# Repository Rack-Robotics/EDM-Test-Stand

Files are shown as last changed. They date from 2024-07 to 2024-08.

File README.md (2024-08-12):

# EDM Test Test

## Summary
This repository contains the documentation and resources for the EDM Test Rig, a test stand developed for advancing Electrical Discharge Machining (EDM) technology. The rig is designed to facilitate the development and testing of EDM components and systems. 

**Subassemblies of EDM Test Rig**
| Subassembly | Description | 
|---|---|
| Frame | Physical 4040 extrusion frame |
| DIN Rail Box | Mounts PSUs and control systems on DIN rails |
| Kinematics | Provides movement of EDM test items | 

## EDM Test Rig Specifications
Specifications of EDM Test rig.
| Specification | Description |
|---|---|
| Approximate Cost  | 2,000 USD |
| Size | 1.4 m x 0.58 m x 1.4 m | 
| Construction | 40x40, 20x20 Extruded Aluminum | 
| Kinematics | C7-Class Ballscrews + NEMA23 Stepper Motors |
| Linear Resolution | +- 30 Microns Maximum | 
| 3D Printer | FDM, Bambu Labs X1C | 
| Power | 120 VAC, 60 Hz |
| Firmware | DangerKlipper | 
| Operating System  | Linux | 
| DIN Rail Space | 40", 35 mm wide, 7.5 mm tall | 
| On-Board Power | 48 VDC, 24 VDC, 12 VDC, 5 VDC |

## Frame 
The frame provides a rigid, industrial grade, structure for conducting testing. 

### Frame Bill of Materials 

Hardware for frame. 
NOTE: 4040 Extrusions must be cut to length
| Item | Description | Quantity | Link | 
|---|---|---|---|
| 4040 Extrusions, Length  500 mm | 4040 Aluminum T-Slot Extrusion | 4 | [Amazon](https://a.co/d/1AEJy0P) |
| 4040 Extrusions, Length  500 mm, Countersunks | Extrusion w/ M5 Countersinks | 2 | [Amazon](https://a.co/d/1AEJy0P) |
| 4040 Extrusions, Length  1000 mm | 4040 Aluminum T-Slot Extrusion | 6 | [Amazon](https://a.co/d/1AEJy0P) |
| 4040 Extrusions, Length  1220 mm | 4040 Aluminum T-Slot Extrusion | 4 | [Amazon](https://a.co/d/1AEJy0P) |
| 4040 L Plate Bracket | M8x16 Brackets for 4040 Exturions | 1 Pack of 8 | [Amazon](https://a.co/d/fb5n5l8) | 
| 4040 L Bracket | Corner Bracket for 4040 Extruions | 1 Pack of 12  | [Amazon](https://a.co/d/0dLhwZp) | 
| 4040 Adjustable Feet | Adjustable feed for 4040 Extruions | 1 Pack of 4 | [Amazon](https://a.co/d/1duonmF) |

## DIN Rail Box
The DIN rail box provides 40 inches of 35 mm x 7.5 mm DIN rail space for mounting power supply units (PSUs), control systems, and other equipment. This setup ensures organized and efficient management of components within the EDM Test Rig.

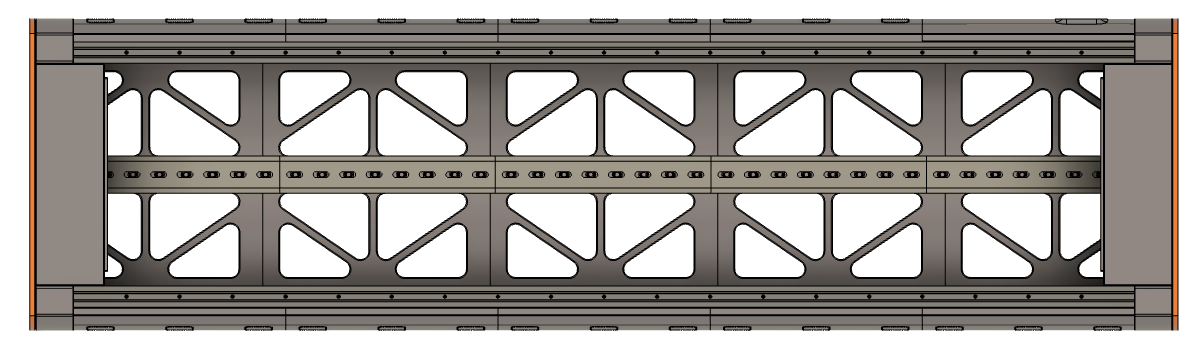
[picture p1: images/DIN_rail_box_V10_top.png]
DIN Rail Box

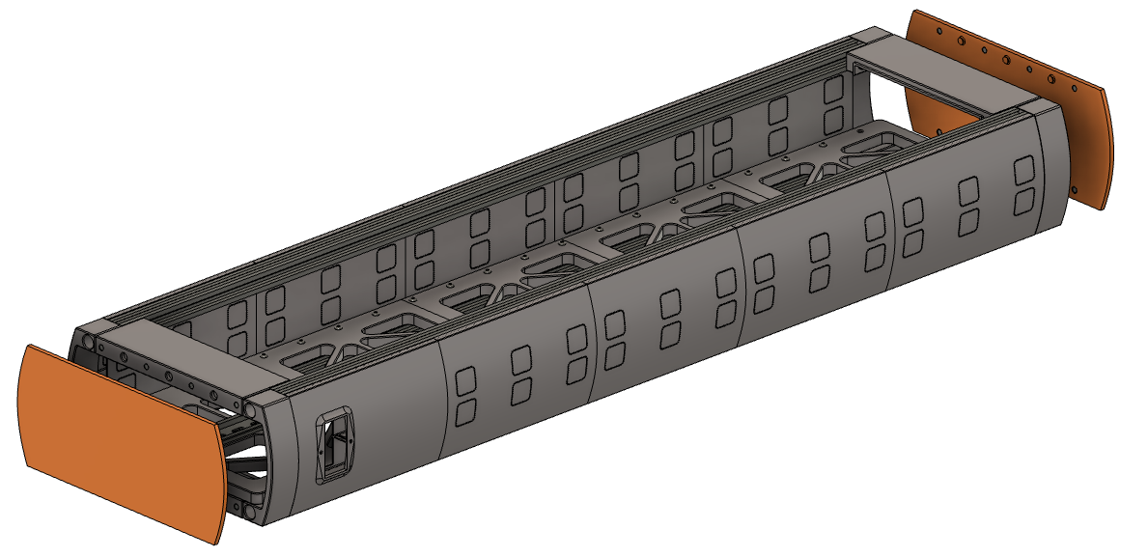
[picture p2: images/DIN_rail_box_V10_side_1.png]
DIN Rail Box


Note: The CAD models for the 2020 aluminum extrusions do not use T-slot nuts, but M4 taps. However, T-slot nuts are recommended.  

### DIN Rail Box Bill of Materials
Required FDM 3D prints for DIN rail box. This project requires several kilograms of filament. Print components with a brim to prevent warping. Enable ironing of top surfaces for base plates for a better surface quality. 
| 3D Prints | Description | Quantity | Material |
|---|---|---|---|
| Base Plate | Connects DIN rails to extrusions | 5 | PLA or ASA |
| Top Spacer | Connects adjacent extrusions | 2 | PLA or ASA |
| End Brace | Braces adjacent extrusions | 4 | PLA or ASA |
| PEM Cover | Mounts PEM module to side | 1 | PLA or ASA |
| Side Cover | Enclosure, with knockouts for wiring | 9 | PLA or ASA |
| End Cover | Enclosure, magnetically retained | 2 | PLA or ASA |

Hardware for DIN rail box: DIN rails, 2020 Aluminum extrusions, & Fasteners. 
| Item | Description | Quantity | Link | 
|---|---|---|---|
| DIN Rails | 35 mm x 7.5 mm, 8" long | 5 | [Amazon](https://a.co/d/1iSyUIB) |
| 2020 Aluminum Extrusion | 1 Meter Length, M6 end taps | 4 | [Amazon](https://a.co/d/0wJvInG) |
| Ruthex M5x9.5 mm Heat Set Insert | Heat set insert for DIN Rails | 15 | [Amazon](https://a.co/d/3ARX3Ab) |
| T-Nuts for 2020 Extrusions | For mounting to 2020 extrusions | 46 | [Amazon](https://a.co/d/hXSw9K0) |
| Neodymium Magnets, 6 mm OD x 2 mm | For magnetic end covers, super glued | 32 | [Amazon](https://a.co/d/eC7ES1e) |
| M6x1 mm, 16 mm Long, DIN 7991 | For 2020 Extrusions & End Spacers | 4 | [McMaster-Carr](https://www.mcmaster.com/91263A838/)  |
| M5x0.5 mm, 10 mm Long, ISO 7380-1 | For DIN rails and Base Plates | 15 | [McMaster-Carr](https://www.mcmaster.com/90943A117/)  | 
| M4x0.7 mm, 12 mm Long, DIN 7991 | For End Braces | 16 | [McMaster-Carr](https://www.mcmaster.com/91263A829/)  |
| M4x0.7 mm, 16 mm Long, ISO 7380 | For mounting base plates to extrusions | 30 | [McMaster-Carr](https://www.mcmaster.com/92095A194/)  |
| M3x0.5 mm. 30 mm Long, DIN 7991 | For PEM module | 2 | [McMaster-Carr](https://www.mcmaster.com/91294A141) |
| M3x0.5 mm Nut, DIN 934 | For PEM module | 2 | [McMaster-Carr](https://www.mcmaster.com/90591A250/)  |

Electronics components for DIN rail box. Includes the control board and computer for running Klipper/DangerKlipper + Linux. 
| Electronics Components | Description | Quantity | Link | 
|---|---|---|---|
| PEM Module | 15A 250V, with Rocker Switch | 1 | [Amazon](https://a.co/d/7NT5VqQ) |
| Meanwell LRS-350-48 | SMPS, 48 VDC | 1 | [Amazon](https://a.co/d/htJ3c0g) |
| Meanwell LRS-350-24 | SMPS, 24 VDC | 1 | [Amazon](https://a.co/d/2wwYgQc) |
| Meanwell LRS-350-12 | SMPS, 12 VDC | 1 | [Amazon](https://a.co/d/iZRj0RO) | 
| Meanwell LRS-100-5 | SMPS. 5 VDC | 1 | [Amazon](https://a.co/d/5YXJFhb) |
| SSR (optional) | 3-32 VDC, 24-480 VAC SSR | 1 | [Amazon](https://a.co/d/i7fY0Kh) |
| NEMA 5-15R Module (optional) | Breakout module for AC interconnects | 1 | [Amazon](https://a.co/d/cqJR1Gi) |
| M4 Ring terminal | 16-22 AWG Crimp, M4 (LRS PSU Terminal) | 100 | [Digikey](https://www.digikey.com/short/3vvnmc7q) |
| 16 AWG Wire, Stranded, Black | For AC & DC interconnects | 25' | [Digikey](https://www.digikey.com/en/products/detail/cnc-tech/1569-16-1-0500-001-1-TS/9450423) |
| 16 AWG Wire, Stranded, White | For AC interconnects | 25' | [Digikey](https://www.digikey.com/en/products/detail/cnc-tech/1569-16-1-0500-002-1-TS/9450424) | 
| 16 AWG Wire, Stranded, Green | For AC interconnects | 25' | [Digikey](https://www.digikey.com/en/products/detail/cnc-tech/1569-16-1-0500-007-1-TS/9450429) | 
| 16 AWG Wire, Stranded, Red | For DC interconnects | 25' | [Digikey](https://www.digikey.com/en/products/detail/cnc-tech/1569-16-1-0500-004-1-TS/9450426) | 
| Manta M5P + CB1 V2.2 Klipper Board | For Klipper/DangerKlipper firmware + Linux | 1 | [Amazon](https://a.co/d/0SYL4TA)

### DIN Rail Accessories
Accessories for mounting hardware to 35 mm x 7.5 mm DIN rails. 

| 3D Prints | Description | Material |
|---|---|---|
| LRS-xxx-48_24_12 | For mounting Meanwell LRS PSUs | PLA or ASA |
| LRS-100-5 | For mounting Meanwell LRS-100-5 PSU | PLA or ASA | 
| Wago 221-415 | For mounting 3x 221-415 Wagos | PLA or ASA |
| Manta M5P | For mounting BTT Manta M5P | PLA or ASA |
| Breadboard 53x165 mm | For mounting medium breadboard | PLA or ASA |
| Omcron SSR | For mounting solid-state relay | PLA or ASA |

### Assembly
- 3D print all required prints out of PLA or ASA 
- Tap ends of 2020 aluminum extrusions with 6x1 mm tap to a depth of at least 8 mm
- Base plates require the insertion of M5x9.5 mm Ruthex inserts using a heat press
- Fasten base plates to 2020 aluminum extrusion using M4 t-slot nuts & M4x0.7 mm 16 mm Long bolts
- Fasten DIN rails to base plate 3D prints using M5x0.7 mm 10 mm long bolts
- Fasten 2020 extrusions together with end brace 3D prints & M6x1 mm 16 mm long bolts
- Space extrusions using space 3D prints and M4x0.7 mm 12 mm long bolts with T-slot nuts
- Fasten PEM module to PEM panel 3D print using M3x0.5 mm 30 mm long bolts and M3x0.5 mm nuts
- Snap on side panel cover 3D prints onto 2020 aluminum extrusions
- Super glue 6 mm OD x 2 mm magnets into end covers and end brace 3D prints. Use soft-blow hammer to assist

### Wiring 
- Wire PEM module AC interconnects to Wago 221-415s on Wago DIN rail 3D print
- Use M4 ring terminals and 16 AWG wire to connect PSUs to AC power
- Connect Manta M5P high-voltage input to LST-350-48 PSU
- Connect Manta DC-in to LRS-350-24 PSU

Notes: 
- Use 16 AWG green wire for AC/EGND interconnects
- Use 16 AWG white wire for AC/Neutral interconnects
- Use 16 AWG black wire for AC/Live & DC/GND nterconnects
- Use 16 AWG red wire for DC/48V, DC/24V, DC/12V, & DC/5V interconnects

## Kinematics
This section details the ballscrew-driven kinematics for the EDM test rig, which ensures precise and controlled movement of test objects.

### Kinematics Bill of Materials

Hardware for kinematics of EDM test rig: Ballscrew actuators. 
| Item | Description | Quantity  | Link |
|---|---|---|---|
| FUYU FSL40 Ballscrew Module, 500mm Stroke | C7 Class ballscrew, 30 micron resolution  | 2 | [Amazon](https://a.co/d/11PDmWa) |
| FUYU FSL40 Ballscrew Module, 1000 mm Stroke | C7 Class ballscrew, 30 micron resolution  | 1 | [Amazon](https://a.co/d/bAsFjcN) |
| LBE-04NU2 PNP NC Endstop | 10 mm x 6 mm, NPN, NC | 2 | Aliexpress |
| M5x0.8 mm, 35 mm Long, DIN 912 | For fastening Y-axis ballscrews to 4040 | 8 | [McMaster-Carr](https://www.mcmaster.com/91292A193/) |
| M5x0.8 mm, 16 mm Long, DIN 7991 | For fastening endstop module | 4 | [Mcmaster-Carr](https://www.mcmaster.com/92125a212/) |
| M3x0.5 mm. 25 mm Long, DIN 7991 | For fastening X-axis brackets | 8 | [Mcmaster-Carr](https://www.mcmaster.com/92125A138/) |
| M3x0.5 mm. 16 mm Long, ISO 7380 | For fastening Y-axis to brackets | 8 | [McMaster-Carr](https://www.mcmaster.com/92095A184/) |
| M3x0.5 mm, 12 mm Long, DIN 7991 | For fastening endstops to endstop print | 2 | [McMaster-Carr](https://www.mcmaster.com/92125A132/) |
| M3x0.5 mm Nut, DIN 934 | For fastening endstops to endstop print | 2 | [McMaster-Carr](https://www.mcmaster.com/90591A250/) |

| 3D Prints | Description | Material |
|---|---|---|
| Left X-Axis Bracket | Connects X-axis to Y-axis | PLA or ASA | 
| Right X-Axis Bracket | Connects X-axis to Y-axis | PLA or ASA | 
| 4040 Endstop Module | Retains magnetic endstop | PLA or ASA | 

### Assembly
Instructions for assembling the kinematic components, including images, will be provided in this section.

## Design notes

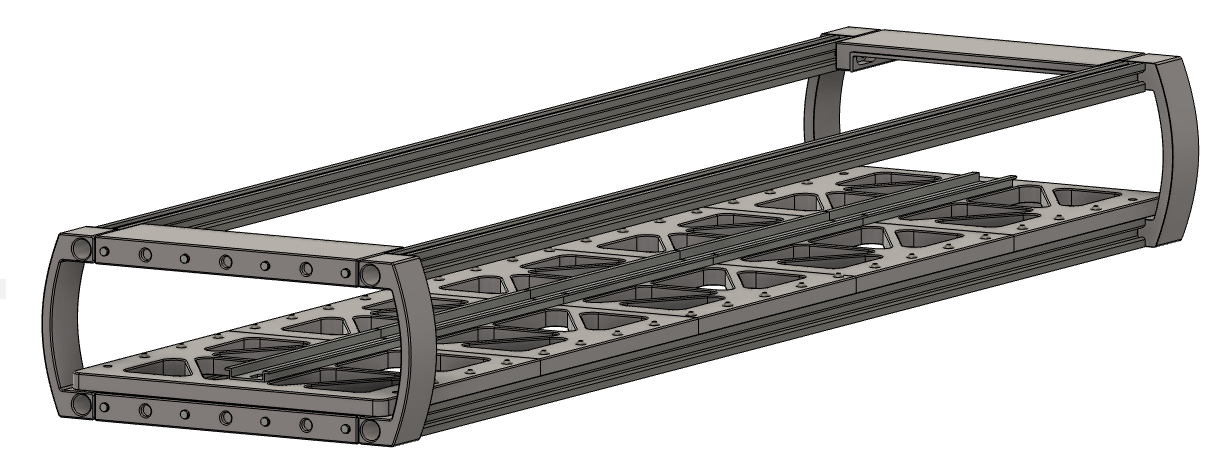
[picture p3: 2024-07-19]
images/DIN_rail_box_V10_side_2.png

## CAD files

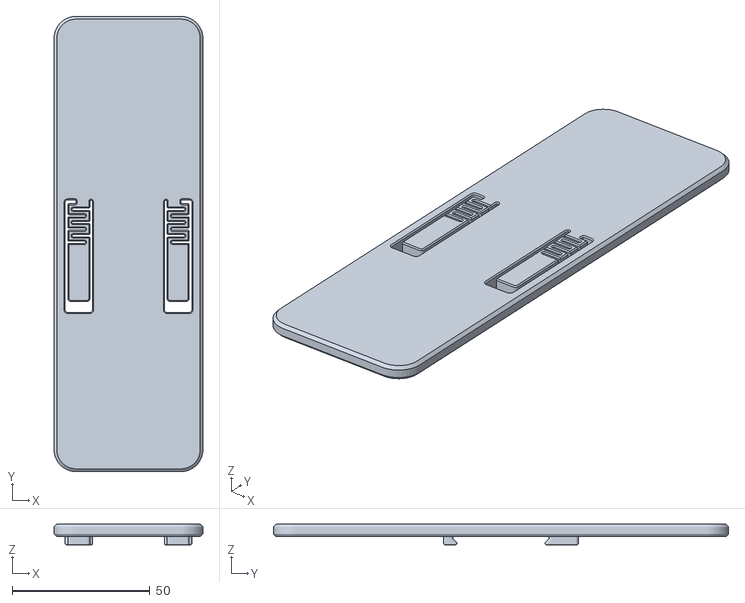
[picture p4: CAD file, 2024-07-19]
DIN rail accessories/breadboard/Breadboard 54x165 mm DIN Rail Mount.stl
54.0 x 165.0 x 7.60

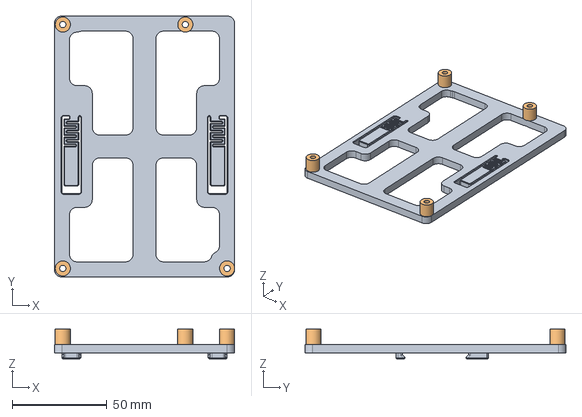
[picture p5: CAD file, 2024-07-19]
DIN rail accessories/Manta M5P/Manta M5P DIN Rail Mount v5.step
95.0 x 137.4 x 15.6 mm

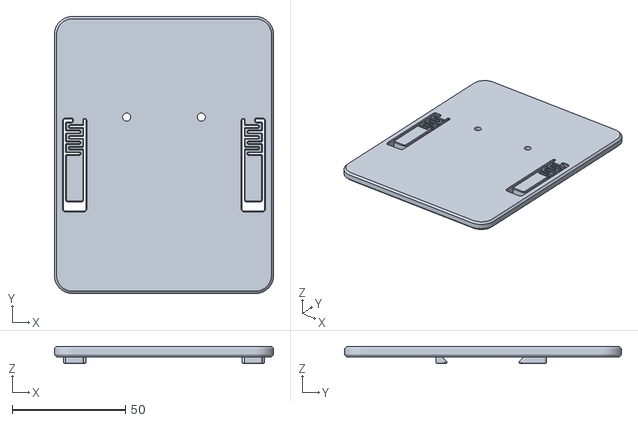
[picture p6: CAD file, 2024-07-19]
DIN rail accessories/Meanwell LRS PSUs/LRS-100-5 DIN Rail Mount.stl
97.0 x 122.5 x 7.60

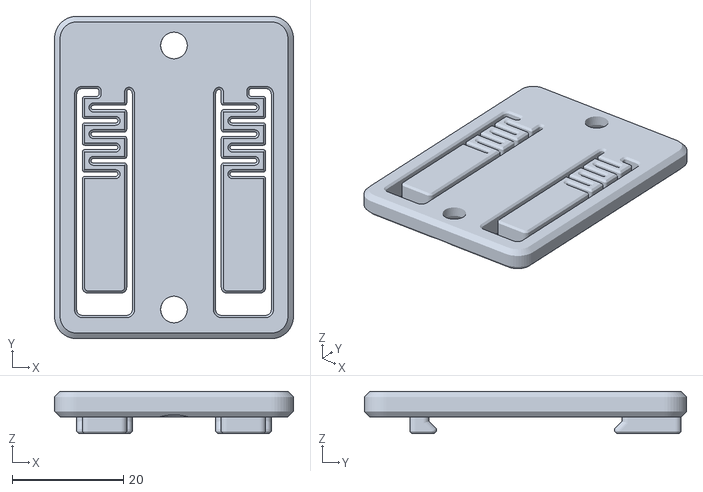
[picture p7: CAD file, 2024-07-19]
DIN rail accessories/OMCRON SSR/LRS-100-5 DIN Rail Mount.stl
43.0 x 58.0 x 7.60

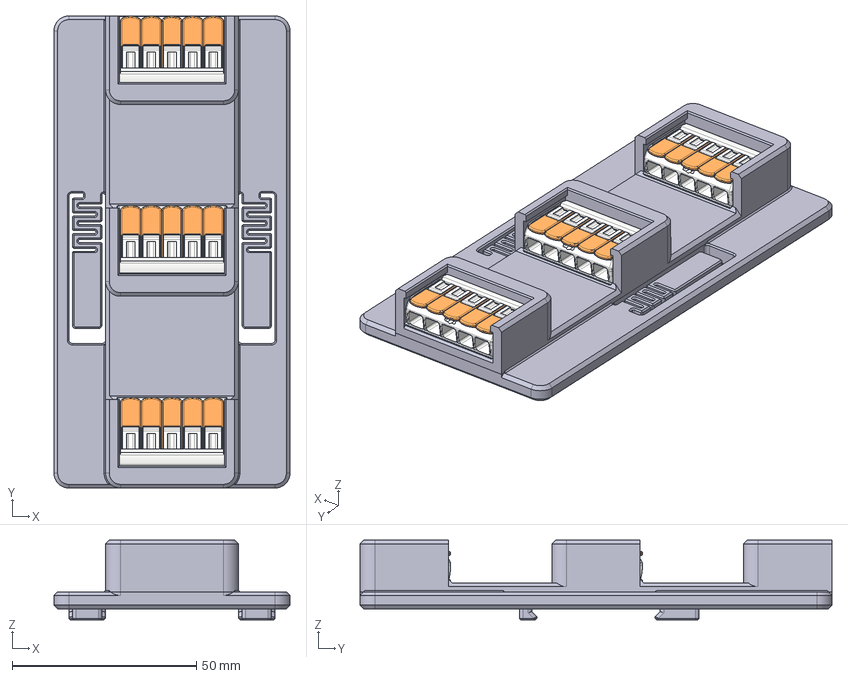
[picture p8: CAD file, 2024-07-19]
DIN rail accessories/wagos/Wago 221-415 DIN Rail Mount v7.step
64.0 x 128.0 x 21.6 mm

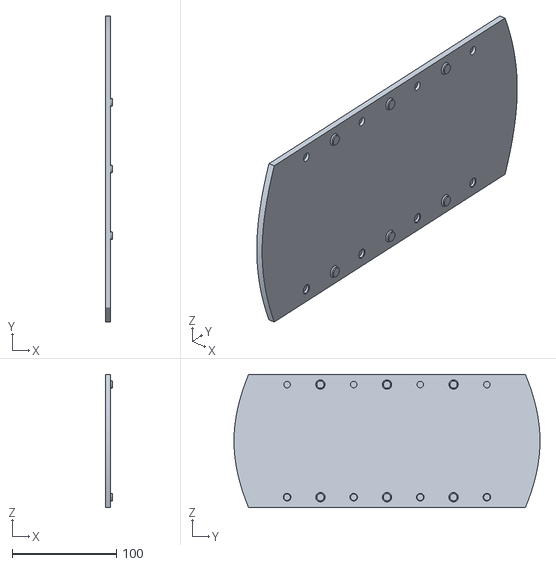
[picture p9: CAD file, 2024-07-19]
DIN rail box/STLs/end cover V10.stl
6.80 x 294.0 x 128.0

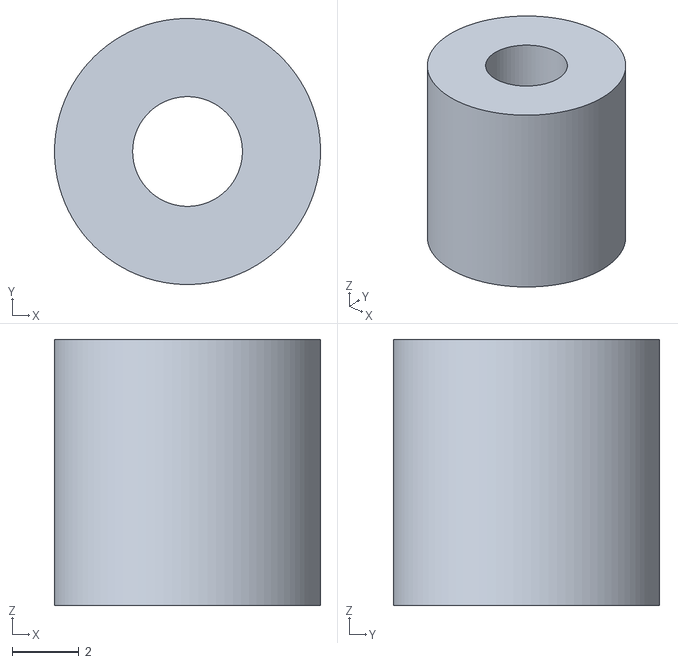
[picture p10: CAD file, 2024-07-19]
DIN rail accessories/Manta M5P/Spacer 1.stl
8.00 x 8.00 x 8.00

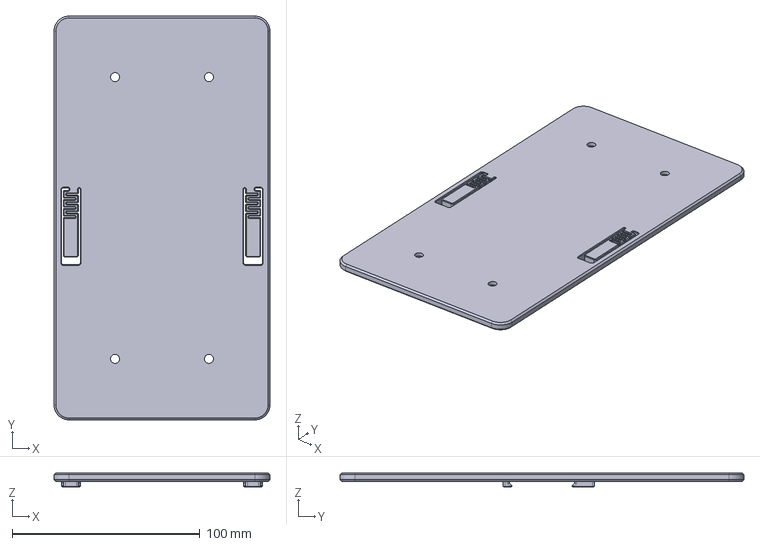
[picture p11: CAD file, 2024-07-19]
DIN rail accessories/Meanwell LRS PSUs/LSR-xxx-48-24-12 DIN Rail Mount v10.step
115.0 x 215.0 x 7.60 mm

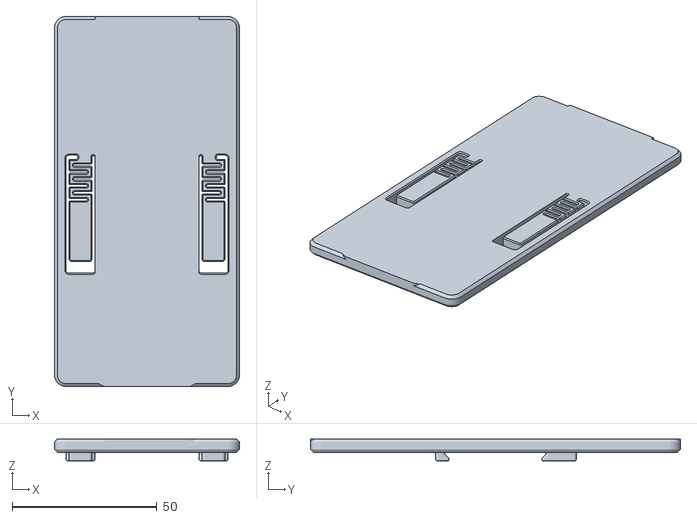
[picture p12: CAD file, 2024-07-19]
DIN rail accessories/wagos/Bottom.stl
64.0 x 128.0 x 7.60

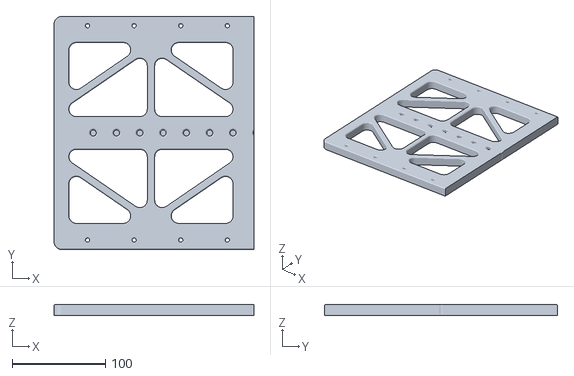
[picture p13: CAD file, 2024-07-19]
DIN rail box/STLs/base plate 1 V10.stl
214.4 x 250.0 x 12.0

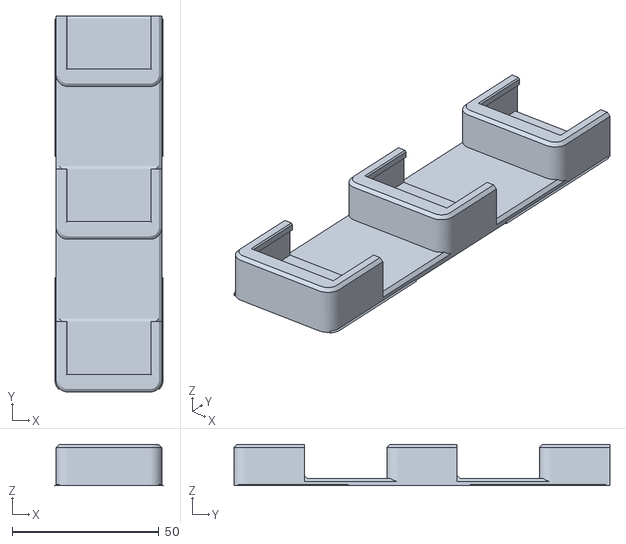
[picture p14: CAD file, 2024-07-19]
DIN rail accessories/wagos/Top.stl
36.8 x 128.0 x 14.0

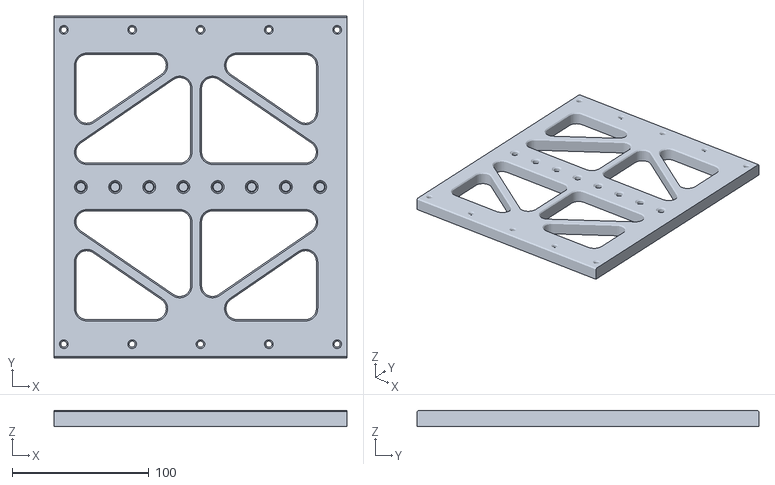
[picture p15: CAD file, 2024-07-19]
DIN rail box/STLs/base plate 3 V10.stl
214.4 x 250.0 x 12.0

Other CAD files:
DIN rail accessories/breadboard/Breadboard 54x165 mm DIN Rail Mount v2.step
DIN rail accessories/OMCRON SSR/SSR DIN Rail Mount v1.step
DIN rail accessories/Manta M5P/Spacer 4.stl
DIN rail accessories/Meanwell LRS PSUs/LRS-100-5 DIN Rail Mount v3.step
DIN rail box/STLs/base plate 5 V10.stl
DIN rail accessories/Manta M5P/Spacer 2.stl
DIN rail accessories/Manta M5P/Manta M8P DIN Rail Mount.stl
DIN rail accessories/Manta M5P/Spacer 3.stl
DIN rail accessories/Meanwell LRS PSUs/LRS-100-5 DIN Rail Mount v3.f3d
DIN rail accessories/Meanwell LRS PSUs/LSR-xxx-48-24-12 DIN Rail Mount v10.f3z
DIN rail accessories/Meanwell LRS PSUs/LSR-xxx-48-24-12 DIN Rail Mount v10.stl
DIN rail accessories/OMCRON SSR/SSR DIN Rail Mount v1.f3d
DIN rail accessories/breadboard/Breadboard 54x165 mm DIN Rail Mount v2.f3d
DIN rail accessories/wagos/Wago 221-415 DIN Rail Mount v7.f3z
DIN rail box/STLs/PEM Cover V10.stl
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

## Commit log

2024-07-19 DIN Rail box V10 files
    added DIN rail box V10 files
    [Bottom.stl, Breadboard 54x165 mm DIN Rail Mount v2.f3d, Breadboard 54x165 mm DIN Rail Mount v2.step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]
2024-07-21 documented DIN rail box
    Added BoM and assembly documentation for DIN rail box.
